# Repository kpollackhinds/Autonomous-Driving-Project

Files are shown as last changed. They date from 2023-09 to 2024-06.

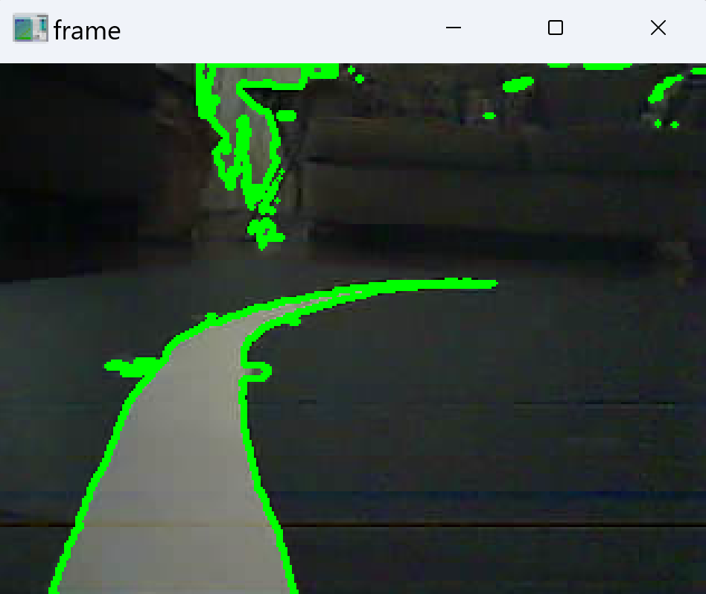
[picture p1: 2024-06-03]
reg_frame.png

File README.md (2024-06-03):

# Autonomous-Driving-Project

Object detection and path following using ESP32 CAM and Wifi Video Streaming

Full documentation available here:
- [Spring 2024 Report (Most recent)](https://www.overleaf.com/read/cvtkfzjbzdcq#cf5f8e)
- [Fall 2023 Report (More detailed mechanical and electrical information)](https://www.overleaf.com/read/jpbfzhhsykrk#73abcc)

## Objective

The goal of this project is to develop an autonomous vehicle that leverages remote computation resources in order to make decisions based on perception. Features will include object detection, path following, and obstacle avoidance.

A primary focus is the development of deep learning methods for the conversion of camera input to motor commands for path following. Traditional computer vision methods for line following are also explored.

## System Layout



### System Description

All communications are perfomed through a Flask based webserver hosted on a laptop. Camera feed from the ESP32 is accessed via an IP address and can be used to display on the frontend, as well as perform computation on the backend. Manual controls can be performed by interfacing with either direction buttons, or a joystick (obtained from https://github.com/bobboteck/JoyStick)

### Operation

Ensure all packages are installed by using _pip install -r requirements.txt_ (Do this in a virtual environment)

For everything to communicate through the web interface, all devices need to be connected to the same wifi network. I defined my network ssid, password and ip in a header file that I did not put on this repository, but you can also specifify by uncommenting the apporpriate place in the [ESP32 Wrover Sketch](https://github.com/kpollackhinds/Autonomous-Driving-Project/blob/main/ESP32/ESP32_Wrover/Sketch_06.2_As_VideoWebServer/Sketch_06.2_As_VideoWebServer.ino):,


and copying and pasting in

```C
#define REMOTE_PORT 5000
const char* ssid = "1234"; // Replace "1234" with your actual SSID
const char* password = "123w4"; // Replace "123w4" with your actual password
const char* ip_address = "***.***.*.***";
```

into the any of the [Arduino Sketches](https://github.com/kpollackhinds/Autonomous-Driving-Project/tree/main/Arduino_wifi/arduino_uno_r4_wifi).

Ensure the source of your video stream is correct in the index.html file in order to see the camera feed.

If all these steps are done, the ESP32 Wrover is powered and **everything is on the same network**, you can run the app.py file using _python web_server app.py --cam 1_ to run with the camera or specifying the arg --cam 0 to run if the camera is not connected. You should see the following output:


Clicking the "Connect to Device" Button will intiate the socket connection to the MCU. The color of the button will change to green once conneted.

There are two different Arduino Sketches used in the [Arduino R4 Wifi Folder](https://github.com/kpollackhinds/Autonomous-Driving-Project/tree/main/Arduino_wifi/arduino_uno_r4_wifi) for training and path tracking method deployment. Either one automatically handles the connection. The model deployment file as of right now only handle the [traditional line contour based line following method](https://www.overleaf.com/project/660e2ea59c73f2049fa892e0#subsubsection.3.3.1:~:text=3.3.1-,Method%20Development,-The%20traditional%20method).

## Parts Used

Different options have been explored for the MCU of the system. Just about any wifi enabled board should be suitable though

- Arduino Uno R4 Wifi (Previously used boards: Raspberry Pi Pico W, Arduino Nano ESP32)
- ESP32 Wrover with OV2640 Cam
- L293D DC Motor Controller (H-Bridge)
- DC Motors (with Encoders)
- 9V Battery for motors
- Power source for Arduino and ESP32 (Power bank)
- QTR-8A Reflectance Array

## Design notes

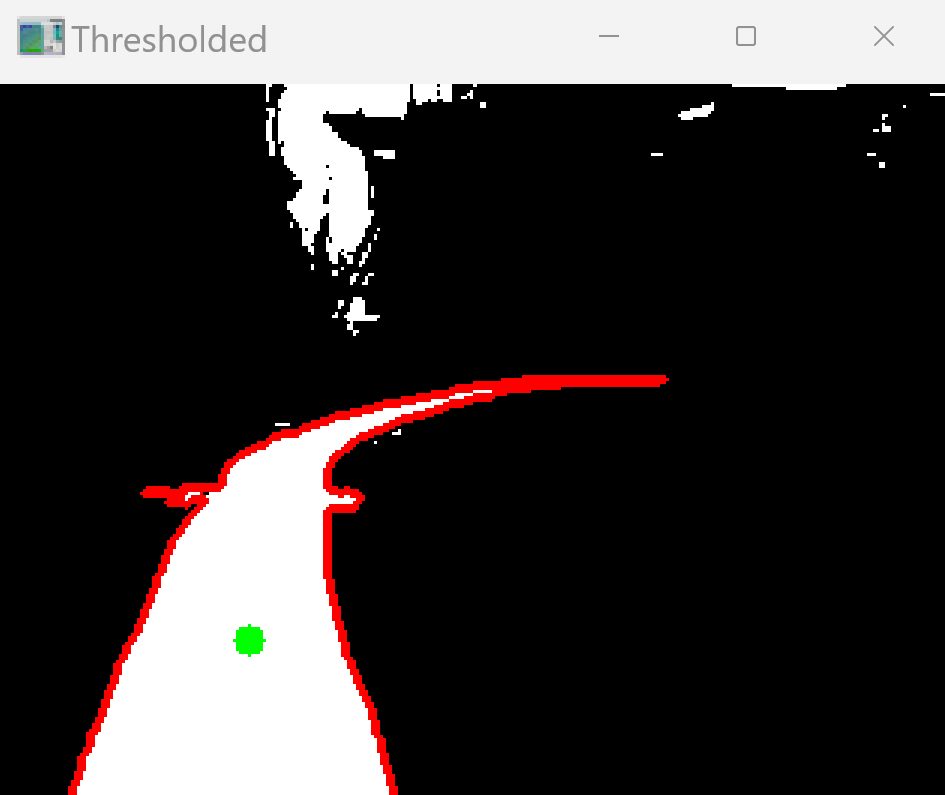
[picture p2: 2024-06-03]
threshold.png

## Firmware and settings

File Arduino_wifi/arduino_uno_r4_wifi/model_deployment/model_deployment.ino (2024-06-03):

//**Notes for next time**//
// add print statements to check if velocities are being sent
// try with camera

//ssid, password and ip_address defined in "secrets.h" files
#include "secrets.h"

#include <WiFiS3.h>
//PID line follower
#include <QTRSensors.h>
#include <sstream>

#define LEFT 0
#define RIGHT 1

// Line Sensor Properties
#define NUM_SENSORS             6  // number of sensors used
#define NUM_SAMPLES_PER_SENSOR  4  // average 4 analog samples per sensor reading
// #define EMITTER_PIN             QTR_NO_EMITTER_PIN  // emitter is controlled by digital pin 2
#define EMITTER_PIN             8  // emitter is controlled by digital pin 8

#define rightMaxSpeed 180 // max speed of the robot
#define leftMaxSpeed 180 // max speed of the robot
#define rightBaseSpeed 90 // this is the speed at which the motors should spin when the robot is perfectly on the line
#define leftBaseSpeed 90 // this is the speed at which the motors should spin when the robot is perfectly on the line

//will determine if we should start training
bool followLine = false;

QTRSensorsAnalog qtra((unsigned char[]) {A5, A4, A3, A2, A1, A0}, NUM_SENSORS, NUM_SAMPLES_PER_SENSOR, EMITTER_PIN);
unsigned int sensorValues[NUM_SENSORS];
const int buttonPin = 12;

const int GOAL = 2400;

//Motor Pin Declarations
  const int motorLeft_Enable = 5;
  const int motorLeft_InputOne = 6;
  const int motorLeft_InputTwo = 7;

  const int motorRight_Enable = 9;
  const int motorRight_InputOne = 10;
  const int motorRight_InputTwo = 11;

//Encoder Pin Declarations
  const int leftENCA = 2;
  const int leftENCB = 4;
  const int rightENCA = 3;
  const int rightENCB = 13;


//Arrays used to make access through function a little easier
const int enca[] = { leftENCA, rightENCA };
const int encb[] = { leftENCB, rightENCB };

long currTime = 0;
long prevTime = 0;

//values accessed/modified within Interrupt
volatile float velocity_i[2] = { 0.0, 0.0 };
volatile long prevT_i[2] = { 0, 0 };

//parameters for low pass filiter
float v1Filt[] = {0,0};
float v1Prev[] = {0,0};

//max number of characters sent per message + null terminator
const byte maxBufferSize = 13; 

//initializing buffer to store characters 
char line[maxBufferSize];

//initializing vector to store commands parsed from lines recieved
int commands[3];  

//initializing token pointer for strtok method
char* token;

//create wifi client object
WiFiClient client;

//function prototypes

bool trad = false;

void stop();
void calibrateLineSensor();
void setMotor(int dir, int pwmVal, int enable, int in1, int in2);
void setMotors(int pwmVal_Left, int pwmVal_Right);

void setup() {
  Serial.begin(115200);
  Serial1.begin(115200);
  delay(10);

  // Initialize line sensor array
  // calibrateLineSensor();

  pinMode(buttonPin, INPUT);

  pinMode(motorLeft_Enable, OUTPUT);
  pinMode(motorLeft_InputTwo, OUTPUT);
  pinMode(motorLeft_InputOne, OUTPUT);

  pinMode(motorRight_Enable, OUTPUT);
  pinMode(motorRight_InputOne, OUTPUT);
  pinMode(motorRight_InputTwo, OUTPUT);

  pinMode(leftENCA, INPUT);
  pinMode(leftENCB, INPUT);
  pinMode(rightENCA, INPUT);
  pinMode(rightENCB, INPUT);

  //interrupt triggered during rising edge of pinA of each encoder
  attachInterrupt(digitalPinToInterrupt(leftENCA), readEncoder<LEFT>, RISING);
  attachInterrupt(digitalPinToInterrupt(rightENCA), readEncoder<RIGHT>, RISING);

  // We start by connecting to a WiFi network
  WiFi.begin(ssid, password);

  Serial.println();
  Serial.println();
  Serial.print("Waiting for WiFi... ");

  while(WiFi.status() != WL_CONNECTED) {
      Serial.print(".");
      delay(500);
  }

  Serial.println("");
  Serial.println("WiFi connected");
  Serial.println("IP address: ");
  Serial.println(WiFi.localIP());

  delay(500);

  Serial.print("Connecting to ");
  Serial.println(ip_address);

  //connecting to socket 
  while (!client.connect(ip_address, REMOTE_PORT)) {
    Serial.println("Connection failed.");
    Serial.println("Waiting a moment before retrying...");
  }

  Serial.println("Connected");
  client.print("Hello\n");
  client.print("This is my IP.\n");
}

void loop() {

  float velocity2[2] = { 0, 0 };

  noInterrupts();
    velocity2[LEFT] = velocity_i[LEFT];
    velocity2[RIGHT] = velocity_i[RIGHT];
  interrupts();
  
  float v2[2] = { velocity2[LEFT] / 960 * 60, velocity2[RIGHT] / 960 * 60 };

  // Low-pass filter (25 Hz cutoff)
  v1Filt[LEFT] = 0.854*v1Filt[LEFT] + 0.0728*v2[LEFT] + 0.0728*v1Prev[LEFT];
  v1Prev[LEFT] = v2[LEFT];

  v1Filt[RIGHT] = 0.854*v1Filt[RIGHT] + 0.0728*v2[RIGHT] + 0.0728*v1Prev[RIGHT];
  v1Prev[RIGHT] = v2[RIGHT];

  currTime = micros();

  // if ((currTime - prevTime)/1e6 >= INTERVAL && followLine){
  //   client.print("_");
  //   client.print(v1Filt[RIGHT]);
  //   client.print(",");
  //   client.print((v1Filt[LEFT])*-1);
  //   client.print("\n");

  //   Serial.println("sent");
  //   prevTime = currTime;

  // }

  if (client.available() > 0) {
    //read back one line from the server
    //reads bytes in until new-line character is seen, stores them in the "line" buffer. Also returns the number of bytes read
    byte size = client.readBytesUntil('\n', line, maxBufferSize);

    line[size] = '\0';  //Null-terminator for the byte array
  }
  // Serial.println(line);

    //check for starting training
  if (strcmp(line, "strt") == 0){
    // Serial1.println("start");
    Serial.println("start");
    followLine = true;
  }

  //check for stopping training
  if (strcmp(line, "stpt") == 0){
    followLine = false;
    trad = false;
    stop();
    Serial.println("stopping sending data");
  }

  if (strcmp(line, "trad") == 0){
    trad = true;
    Serial.println("Starting traditional method");
  }

  if (trad){
    float leftMotorSpeed = 0.0, rightMotorSpeed = 0.0;

    char* token = strtok(line, ",");
    if (token != NULL) {
        leftMotorSpeed = atof(token);
        token = strtok(NULL, ",");
        if (token != NULL) {
            rightMotorSpeed = atof(token);
            Serial.print("Left Motor Speed: ");
            Serial.println(leftMotorSpeed);
            Serial.print("Right Motor Speed: ");
            Serial.println(rightMotorSpeed);

            setMotors((int)leftMotorSpeed, (int)rightMotorSpeed);
        // } else {
        //     // Serial.println("Failed to parse right motor speed");
        // }
            } 
    // else {
    //     // Serial.println("Failed to parse left motor speed");
    // }

    // Print the buffer to verify content
    // Serial.print("Received line: ");
    // Serial.println(line);
    }
  }
  // if (followLine){
  //   // Get line position
  //   unsigned int position = qtra.readLine(sensorValues, QTR_EMITTERS_ON, 1);

  //   // Compute error from line
  //   int error = GOAL - position;

  //   // Compute motor adjustment
  //   int adjustment = KP*error + KD*(error - lastError);

  //   // Store error for next increment
  //   lastError = error;

  //   // Adjust motors 
  //   int rightMotorSpeed = rightBaseSpeed + adjustment;
  //   int leftMotorSpeed = leftBaseSpeed - adjustment;

  //   if (rightMotorSpeed > rightMaxSpeed ) rightMotorSpeed = rightMaxSpeed; // prevent the motor from going beyond max speed
  //   if (leftMotorSpeed > leftMaxSpeed ) leftMotorSpeed = leftMaxSpeed; // prevent the motor from going beyond max speed
  //   if (rightMotorSpeed < 0) rightMotorSpeed = 0; // keep the motor speed positive
  //   if (leftMotorSpeed < 0) leftMotorSpeed = 0; // keep the motor speed positive

  //   setMotors(leftMotorSpeed, rightMotorSpeed);
  // }

  //manual button commands using default speed of 50
  if (followLine == false){
    if (strcmp(line, "stp") == 0){
      stop();
    }
  }
    
  //reset the line array to an array of zeros in the buffer size
  memset(line, 0, maxBufferSize);

  if (client.connected () == 0) {
    client.stop();
    WiFi.disconnect();
    WiFi.begin(ssid, password);

    while(WiFi.status() != WL_CONNECTED) {
        Serial.print(".");
        delay(500);
    }

    Serial.println("");
    Serial.println("WiFi connected");
    Serial.println("IP address: ");
    Serial.println(WiFi.localIP());

    delay(500);

    Serial.print("Connecting to ");
    Serial.println(ip_address);

    //connecting to socket 
    while (!client.connect(ip_address, REMOTE_PORT)) {
      Serial.println("Connection failed.");
      Serial.println("Waiting a moment before retrying...");
    }

    Serial.println("Connected");

  } 
  
  delay(1); //delay used to set a fixed sampling rate for low pass filter
}

//read encoder function checks speed and direction of motor. Gets triggered by interrupt defined in setup
template<int j>
void readEncoder() {
  int b = digitalRead(encb[j]);
  int increment = 0;
  if (b > 0) {
    increment = 1;
  } else {
    increment = -1;
  }

  long currT = micros();
  float deltaT = (float)(currT - prevT_i[j]) / 1000000;

  velocity_i[j] = increment / deltaT;

  prevT_i[j] = currT;
}

void setMotor(int pwmVal, int enable, int in1, int in2, int dir = 1) {
  analogWrite(enable, pwmVal);
  if (dir == 1) {
    digitalWrite(in2, LOW);
    digitalWrite(in1, HIGH);
  } else if (dir == -1) {
    digitalWrite(in1, LOW);
    digitalWrite(in2, HIGH);
  } else {
    digitalWrite(in1, LOW);
    digitalWrite(in2, LOW);
  }
}

void setMotors(int pwmVal_Left, int pwmVal_Right) {
  Serial.println(pwmVal_Right);
  digitalWrite(motorRight_InputOne, HIGH);
  digitalWrite(motorRight_InputTwo, LOW);
  analogWrite(motorRight_Enable, pwmVal_Right);
  digitalWrite(motorLeft_InputOne, LOW);
  digitalWrite(motorLeft_InputTwo, HIGH);
  analogWrite(motorLeft_Enable, pwmVal_Left);
}

void stop() {
  Serial.println("PAUSE");
  digitalWrite(motorLeft_InputOne, LOW); 
  digitalWrite(motorLeft_InputTwo, LOW); 
  digitalWrite(motorRight_InputOne, LOW); 
  digitalWrite(motorRight_InputTwo, LOW); 
}

void calibrateLineSensor() {
  delay(500);
  pinMode(13, OUTPUT);
  digitalWrite(13, HIGH);    // turn on Arduino's LED to indicate we are in calibration mode
  for (int i = 0; i < 3000; i++)  // make the calibration take about 10 seconds
  {
    qtra.calibrate();       // reads all sensors 10 times at 2.5 ms per six sensors (i.e. ~25 ms per call)
  }
  digitalWrite(13, LOW);     // turn off Arduino's LED to indicate we are through with calibration
  Serial.println("done");
}

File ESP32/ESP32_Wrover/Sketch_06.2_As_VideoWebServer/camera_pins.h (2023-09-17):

#if defined(CAMERA_MODEL_WROVER_KIT)
#define PWDN_GPIO_NUM    -1
#define RESET_GPIO_NUM   -1
#define XCLK_GPIO_NUM    21
#define SIOD_GPIO_NUM    26
#define SIOC_GPIO_NUM    27

#define Y9_GPIO_NUM      35
#define Y8_GPIO_NUM      34
#define Y7_GPIO_NUM      39
#define Y6_GPIO_NUM      36
#define Y5_GPIO_NUM      19
#define Y4_GPIO_NUM      18
#define Y3_GPIO_NUM       5
#define Y2_GPIO_NUM       4
#define VSYNC_GPIO_NUM   25
#define HREF_GPIO_NUM    23
#define PCLK_GPIO_NUM    22

#else
#error "Camera model not selected"
#endif

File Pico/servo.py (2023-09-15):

from machine import Pin, PWM
from time import sleep

class Servo:

    """ A simple class for controlling a 9g servo with the Raspberry Pi Pico.
 
        Attributes:
 
        minVal: An integer denoting the minimum duty value for the servo motor.
 
        maxVal: An integer denoting the maximum duty value for the servo motor.
    """
     
    def __init__(self, pin: int, minVal = 1000000, maxVal = 2000000, midVal = 1500000):
        
        self.minVal = minVal
        self.midVal = midVal
        self.maxVal = maxVal

        self.pwm = PWM(Pin(pin))
        self.pwm.freq(50)
        self.pwm.duty_ns(self.midVal)

    def go(self, speed):
        if speed == 0:
            self.pwm.duty_ns(self.midVal)
        
        elif speed > 100:
            self.pwm.duty_ns(self.maxVal)
        
        elif speed < -100:
            self.pwm.duty_ns(self.minVal)
        
        else:
            #mapping input to duty cycle time in nano seconds
            self.value = int(((speed - (-100)) / (100 - (-100)) * (self.maxVal - self.minVal)) + self.minVal)
            self.pwm.duty_ns(self.value)

"""
basic controls for servo motions
"""
class Controls:
    def __init__(self, rightServo: Servo, leftServo: Servo) -> None:
        self.rightServo = rightServo
        self.leftServo = leftServo

    #duration in ms
    def forward(self, duration = None, speed = 50):
        self.rightServo.go(speed)
        self.leftServo.go(speed)

    def backward(self, duration = None, speed = -50):
        if speed >0:
            speed = speed *-1

        self.rightServo.go(speed)
        self.leftServo.go(speed)

    #ratio = speed of "passive" wheel (right wheel if turning right, etc)/ speed of active wheel
    #if ratio is 1, they are turning at the same speed in opposite directions
    def right(self, duration = None, ratio = 1.0, active_wheel_speed = 50):
        self.right_speed = int(-1* ratio * active_wheel_speed)
        
        self.rightServo.go(self.right_speed)
        self.leftServo.go(active_wheel_speed)

    def left(self, duration = None, ratio = 1.0, active_wheel_speed = 50):
        self.left_speed = int(-1* ratio * active_wheel_speed)
        
        self.rightServo.go(active_wheel_speed)
        self.leftServo.go(self.left_speed)

    def stop(self):
        self.rightServo.go(0)
        self.leftServo.go(0)

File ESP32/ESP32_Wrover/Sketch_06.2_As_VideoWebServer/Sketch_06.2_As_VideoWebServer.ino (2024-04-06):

#include "esp_camera.h"
#include "secrets.h"
#include <WiFi.h>
//
// WARNING!!! PSRAM IC required for UXGA resolution and high JPEG quality
//            Ensure ESP32 Wrover Module or other board with PSRAM is selected
//            Partial images will be transmitted if image exceeds buffer size
//

// Select camera model
#define CAMERA_MODEL_WROVER_KIT // Has PSRAM
#include "camera_pins.h"

//BELOW IS ONLY FOR REFERENCE//
// typedef enum {
//     FRAMESIZE_96X96,    // 96x96
//     FRAMESIZE_QQVGA,    // 160x120
//     FRAMESIZE_QCIF,     // 176x144
//     FRAMESIZE_HQVGA,    // 240x176
//     FRAMESIZE_240X240,  // 240x240
//     FRAMESIZE_QVGA,     // 320x240
//     FRAMESIZE_CIF,      // 400x296
//     FRAMESIZE_HVGA,     // 480x320
//     FRAMESIZE_VGA,      // 640x480
//     FRAMESIZE_SVGA,     // 800x600
//     FRAMESIZE_XGA,      // 1024x768
//     FRAMESIZE_HD,       // 1280x720
//     FRAMESIZE_SXGA,     // 1280x1024
//     FRAMESIZE_UXGA,     // 1600x1200
//     // 3MP Sensors
//     FRAMESIZE_FHD,      // 1920x1080
//     FRAMESIZE_P_HD,     //  720x1280
//     FRAMESIZE_P_3MP,    //  864x1536
//     FRAMESIZE_QXGA,     // 2048x1536
//     // 5MP Sensors
//     FRAMESIZE_QHD,      // 2560x1440
//     FRAMESIZE_WQXGA,    // 2560x1600
//     FRAMESIZE_P_FHD,    // 1080x1920
//     FRAMESIZE_QSXGA,    // 2560x1920
//     FRAMESIZE_INVALID
// } framesize_t;

// defined in secrets.h file
// const char* ssid     = "********";   //input your wifi name
// const char* password = "********";   //input your wifi passwords

void startCameraServer();

void setup() {
  Serial.begin(115200);
  Serial.setDebugOutput(true);
  Serial.println();

  camera_config_t config;
  config.ledc_channel = LEDC_CHANNEL_0;
  config.ledc_timer = LEDC_TIMER_0;
  config.pin_d0 = Y2_GPIO_NUM;
  config.pin_d1 = Y3_GPIO_NUM;
  config.pin_d2 = Y4_GPIO_NUM;
  config.pin_d3 = Y5_GPIO_NUM;
  config.pin_d4 = Y6_GPIO_NUM;
  config.pin_d5 = Y7_GPIO_NUM;
  config.pin_d6 = Y8_GPIO_NUM;
  config.pin_d7 = Y9_GPIO_NUM;
  config.pin_xclk = XCLK_GPIO_NUM;
  config.pin_pclk = PCLK_GPIO_NUM;
  config.pin_vsync = VSYNC_GPIO_NUM;
  config.pin_href = HREF_GPIO_NUM;
  config.pin_sscb_sda = SIOD_GPIO_NUM;
  config.pin_sscb_scl = SIOC_GPIO_NUM;
  config.pin_pwdn = PWDN_GPIO_NUM;
  config.pin_reset = RESET_GPIO_NUM;
  config.xclk_freq_hz = 20000000;
  config.pixel_format = PIXFORMAT_JPEG;
  
  // if PSRAM IC present, init with UXGA resolution and higher JPEG quality
  //                      for larger pre-allocated frame buffer.
  if(psramFound()){
    config.frame_size = FRAMESIZE_UXGA;
    // config.frame_size = FRAMESIZE_HVGA;
    // config.frame_size = FRAMESIZE_QVGA;
    // config.frame_size = FRAMESIZE_240X240; //this one
;
    config.jpeg_quality = 10;
    // config.jpeg_quality = 15;

    config.fb_count = 2;
  } else {
    config.frame_size = FRAMESIZE_SVGA; //this one
    // config.frame_size = FRAMESIZE_UXGA; 

    // config.jpeg_quality = 30;
    config.jpeg_quality = 15;

    config.fb_count = 1;
  }

  // camera init
  esp_err_t err = esp_camera_init(&config);
  if (err != ESP_OK) {
    Serial.printf("Camera init failed with error 0x%x", err);
    return;
  }

  sensor_t * s = esp_camera_sensor_get();
  // drop down frame size for higher initial frame rate
  // s->set_framesize(s, FRAMESIZE_VGA);
  s->set_framesize(s, FRAMESIZE_QVGA);
    // s->set_framesize(s, FRAMESIZE_240X240); //this one


  WiFi.begin(ssid, password);

  while (WiFi.status() != WL_CONNECTED) {
    delay(500);
    Serial.print(".");
  }
  Serial.println("");
  Serial.println("WiFi connected");

  startCameraServer();

  Serial.print("Camera Ready! Use 'http://");
  Serial.print(WiFi.localIP());
  Serial.println("' to connect");
}

void loop() {
  // put your main code here, to run repeatedly:
  delay(10000);
}

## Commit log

2023-09-11 adding video streaming code for esp32 cam
2023-09-14 added code for PWM speed control of servo motors
2023-09-15 created basic servo motor control library for Raspberry Pi Pico
2023-09-17 added event listener for buttons
2023-09-17 added code for esp32 video streaming
2023-09-18 successful socket connection between pico client and local machine server
2023-09-19 added additional functionality to buttons, and incorporated commands to pico
2023-09-19 got camera feed in opencv
2023-09-20 updated socket connection procedure on pico client end
2023-10-01 added sending controls to pico
2023-10-10 added dc motor controls and tcp comms for arduino
2023-10-11 mapped joystick controls to motor speeds and directions
2023-10-21 added automatic image saving at fixed intervals
    [Sketch_06.2_As_VideoWebServer.ino, main.py]
2023-11-17 two motor pid speed control added
2023-11-24 added new training algorithm and reflectance sensor line following code
2023-12-07 added training pipeline using QTR-8A reflectance sensor
2024-02-24 fixed issue with image saving
    [fritzing.fzz, pid_no_filter.csv, pid_no_filter_copy.csv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]
2024-02-24 removing extra stuff
    [pid_no_filter.csv, pid_no_filter_copy.csv, pid_w_filter.csv]
2024-04-06 updated frame capture and data sending
2024-04-30 added front-end elements and arduino code for model deployment
2024-06-03 Remove arduino esp32 folder from repository
